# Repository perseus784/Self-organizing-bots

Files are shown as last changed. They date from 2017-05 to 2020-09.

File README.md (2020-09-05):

# About  

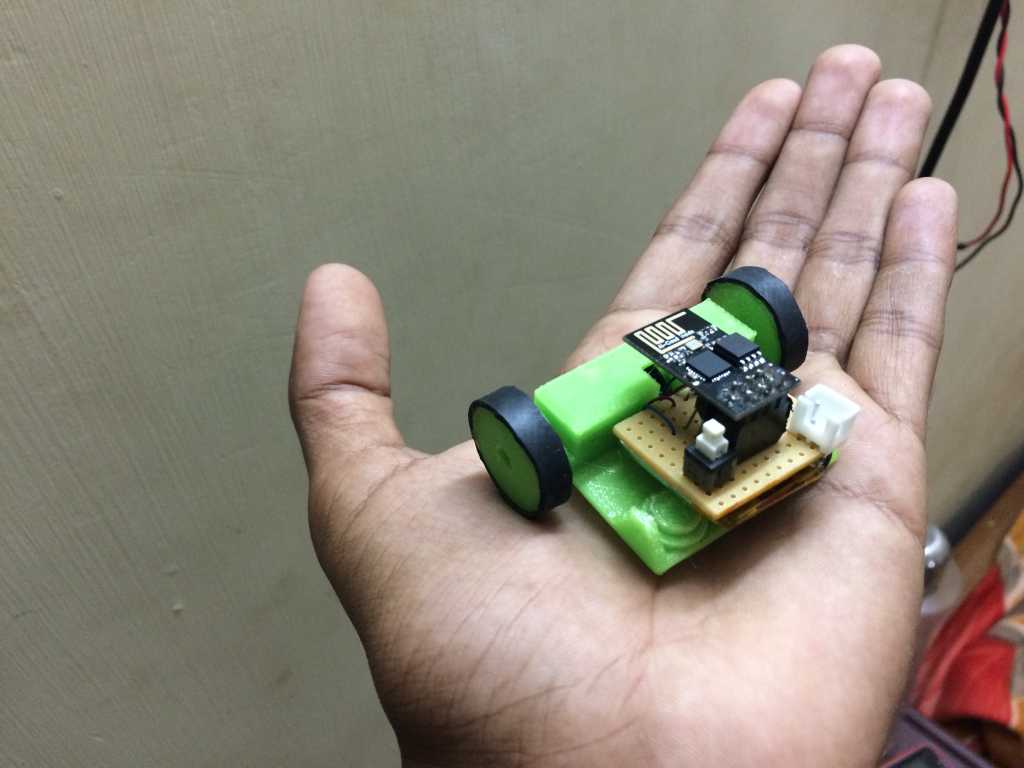
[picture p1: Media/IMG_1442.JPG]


A group of small robots capable of assembling themselves built using ESP8266 wifi module and Python.
The platform consists of a collection of custom-designed wheeled robots each 41x35 mm in dimensions, a Wi-Fi module, and object tracking using image processing techniques. They are controlled by custom written algorithms and python libraries. The project illustrates the potential of group interface through a set of algorithms implemented with custom designed robots, and discuss general design considerations unique to collective intelligence.

## Design Consideration:
 All the parts, modelling, circuits were mainly based on the making the robot as small as possible with the technology that is available in the vicinity. It was constrained by cost, time and availability of the hardware in the geography. Most of the struggle and research went into choosing and making the parts as simple and effective as possible. The finalized design was a product of numerous iteration of protypes in software and hardware level. Making the circuitary small at the same time not too heavy for the motor was a challenge and even that went through a lot of prototyping and expermentation. 
 
<br> 

# Key Features:
* 41x35 mm in dimensions.
* Controlled using WiFi.
* Cheap (around $25). Maybe even cheaper if mass produced.
* 3D files provided.
* Contour tracking
* Path planning
* Simple circuit design

## EXISTING SYSTEM:  
**Zooids:** The project is executed by students of Stanford University. The system introduced swarm user interfaces; It is an open-source open-hardware platform for developing tabletop swarm interfaces. It consists of a collection of custom-designed wheeled micro robots each 2.6 cm in diameter, a radio base-station, a high speed DLP structured light projector for optical tracking, and a software framework for application development and control.

**Kilobots:** Kilobots are done by students of Harvard University. Kilobots should be operated on a smooth, flat surface to ensure proper robot mobility. To aid communication, the surface should be glossy or reflective. The robots beneath the overhead controller in a about a one meter diameter region will be able to receive messages.

## PROPOSED SYSTEM:

On basis of the above survey and after referring various technical papers a new and innovative project idea was developed. The aim of the project "Self organized robots" was to build a group of robots which would construct an input schematic given by the user on a given platform.

The project included study of various fields in Electronics and Computer Science such as Machine Learning, Collective Intelligence, Embedded Systems, Wireless Sensor Networks and Computer Networks. It included Wireless communication between the robots. It consisted of a group or swarm of robots which were guided by a server using various algorithms programmed in its micro-controller. The robot tracking is done by using image processing technique.

## TOOLS

The greatest difficulty faced in the whole system is to make the size of each robot as small as possible. It required building custom designs for the robots and rapid prototyping is employed for the modifications based on practical implementations.

## Hardware

### Battery

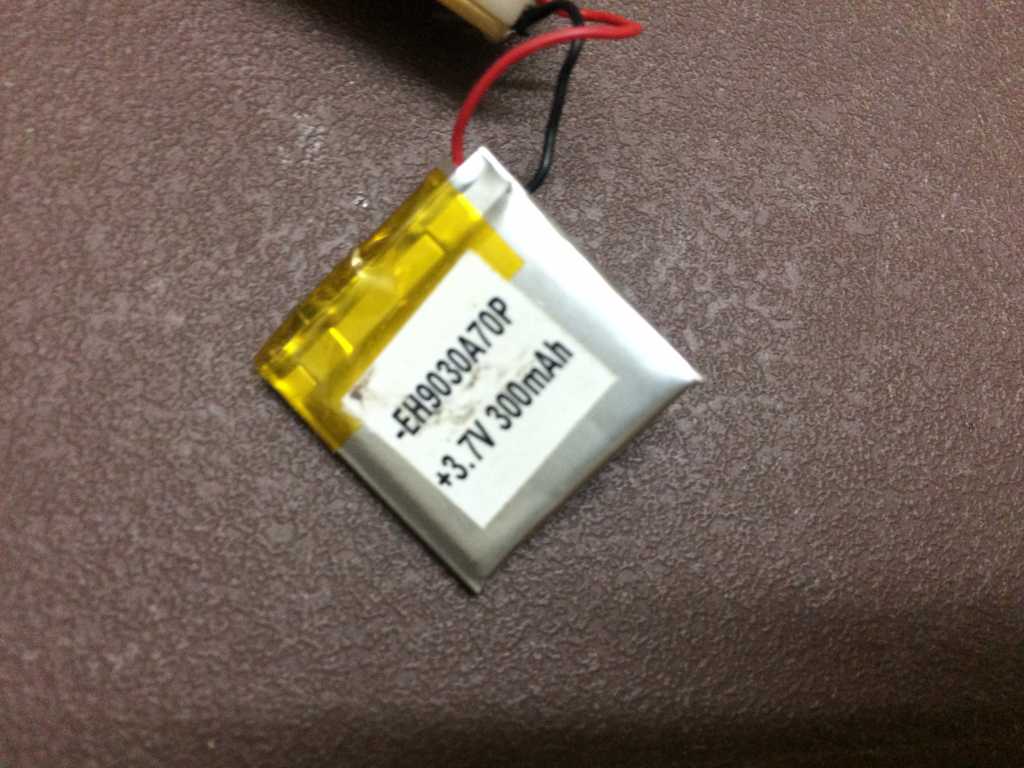
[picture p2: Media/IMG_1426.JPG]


A  Rechargeable Lithium-Polymer battery cell is used to power the entire robot. It has the technical specifications of 3.7v with 200mAh capacity and 20C discharge rate. This optimum design of battery not only helps in keeping the robotic structure  in less weight and small size but also supplies required power efficiently. A single charge of the battery can run the robot for around 20 minutes of continues usage and 1 hour of idle standby. 
<br>

### Coreless DC motor

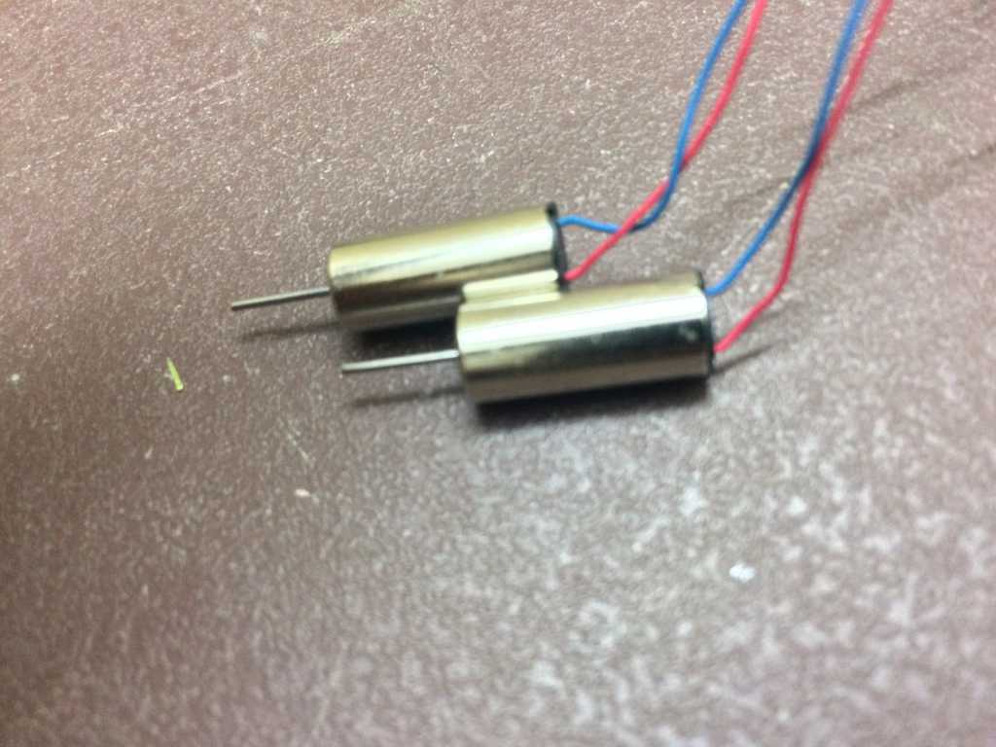
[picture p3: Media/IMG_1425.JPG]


Two coreless DC motors are being employed since it is a two wheeled robot. This two wheeled construction of the robot gives it a 3-degree locomotion i.e. it can move in forward, right and left directions. The motor’s specifications are 3.3v and 0.1A. The motor is specifically selected for its high acceleration and smaller size. It is of size 16*7mm in dimensions.   
<br>

### ESP8266 Wi-Fi Controller

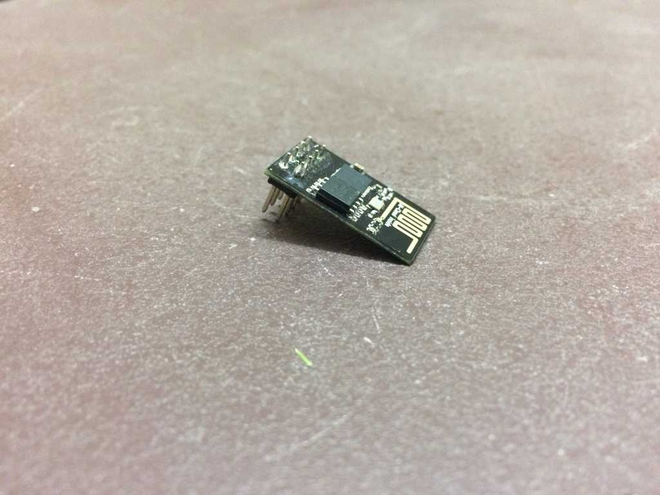
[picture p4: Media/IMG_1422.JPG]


The ESP8266 Wi-Fi Module is a self contained Microcontroller with inbuilt Wi-Fi options. It can establish new networks and also able to connect to already available networks. It has a very compact design with two GPIO pins which makes it the most suitable board for this project. It can be easily programmed by C language Arduino IDE.  
<br>

### BS170 N-Channel MOSFET

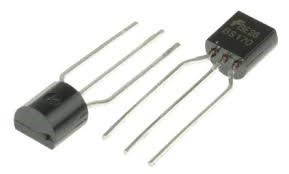
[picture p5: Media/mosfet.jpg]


The BS170 is a logic level MOSFET, which is capable of showing qualities of the higher rating MOSFETs in small signal applications. This property of it used to select it for the switching purpose of the motor using the microcontroller. It has a specification of Vds= 60v and Id= 500 mA.  
<br>

## Software level stuff:
* Python
* Matplotlib
* OpenCV
* Algorithms
* Swarm algorithms
* Socket programming -web services
* Arduino esp8266 programming
* Structural algos
* Clustering
* KNN
* Heirarchical clustering

## 3D Printing 

### SolidWorks Software



SolidWorks is a solid modeler, and utilizes a parametric feature-based approach to create models and assemblies. Building a model in SolidWorks usually starts with a 2D sketch and 3D model can be derived later. The sketch consists of geometry such as points, lines, arcs, and spines. Dimensions are added to the sketch to derive the required 3D model.
The 3D model based on the spatial requirements which has been done using the SolidWorks software is displayed below,

3D Printing is done using 3D Printer. The 3D printer used for prototyping is WANHAO Duplicator. The WANHAO Duplicator makes solid, three-dimensional objects out of melted WANHAO PLA (PolyLactic Acid) Filament. 3D model derived from SolidWorks is translated into instructions for the WANHAO Duplicator and sent to the machine via USB cable or SD Card. Then the WANHAO Duplicator heats the WANHAO PLA Filament and squeezes it out through a nozzle to make a solid object layer by layer. This technique is called fused deposition modeling (FDM).

<p align="left">
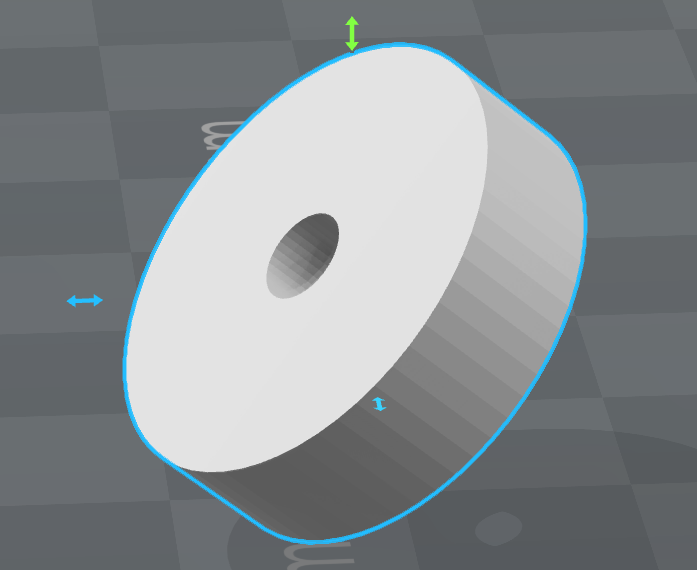
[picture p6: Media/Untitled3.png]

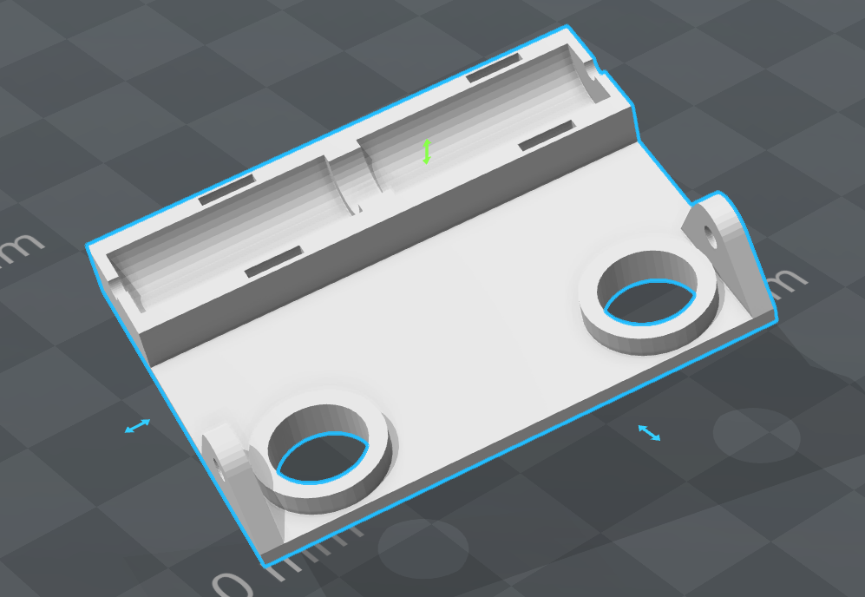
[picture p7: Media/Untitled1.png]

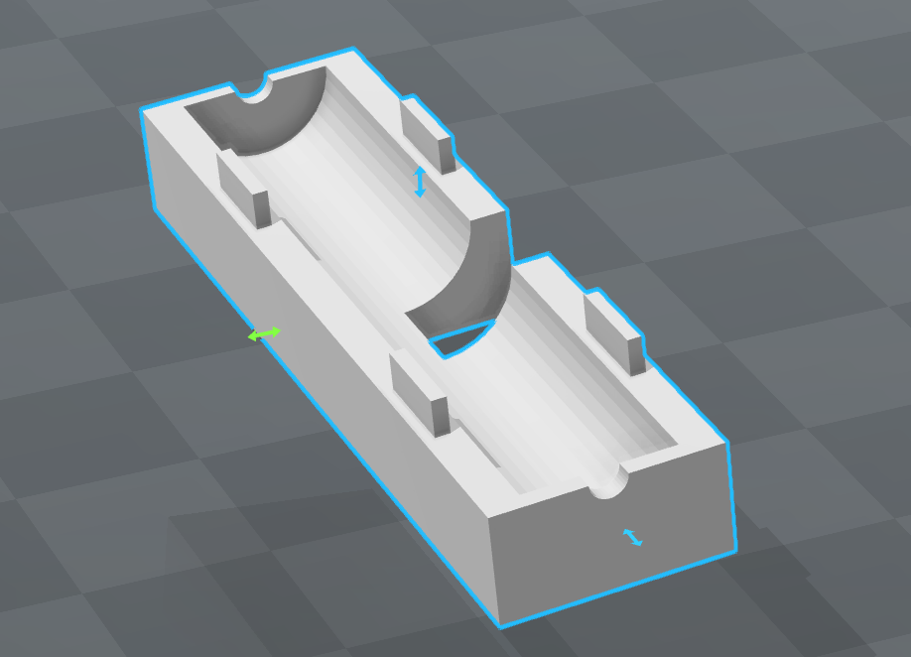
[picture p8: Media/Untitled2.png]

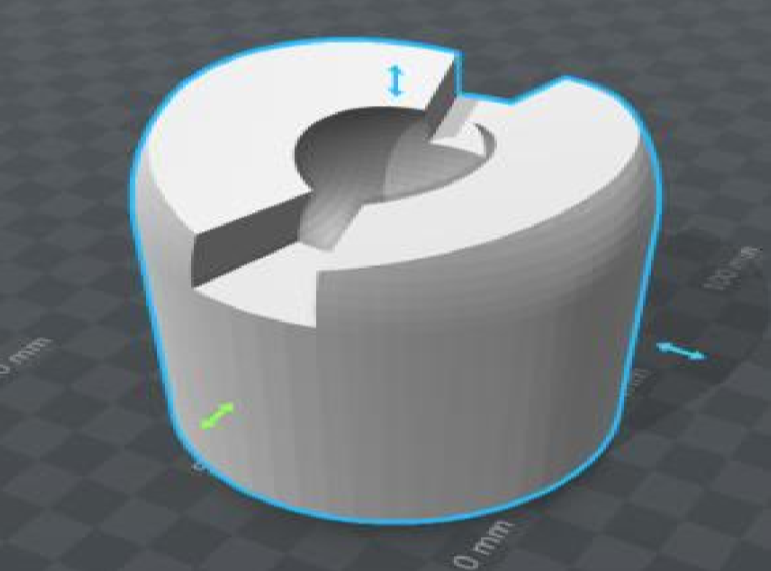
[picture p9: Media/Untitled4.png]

</p>

### Circuit Design

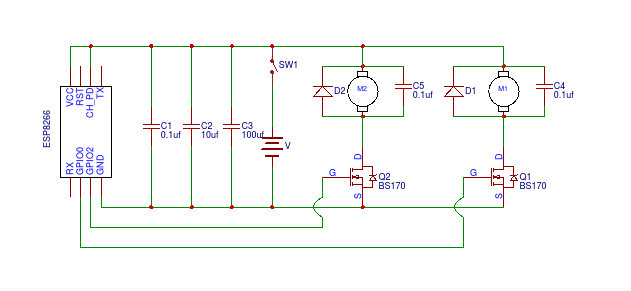
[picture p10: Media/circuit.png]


The circuit is designed mainly on the consideration of simplicity and smallest size possible. So, very basic components are only used in the electrical circuit.

## IMPLEMENTATION

### Hardware Implementation

**3D printed parts ready for assembly:**
                                                                                                                                      
<p align="left">
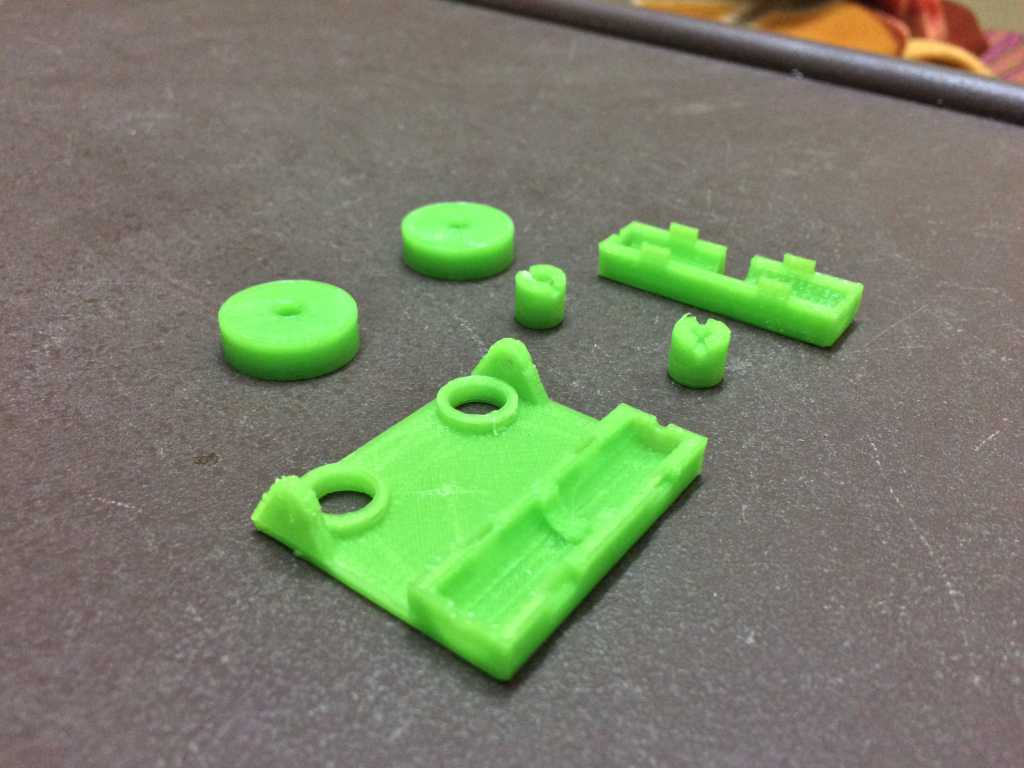
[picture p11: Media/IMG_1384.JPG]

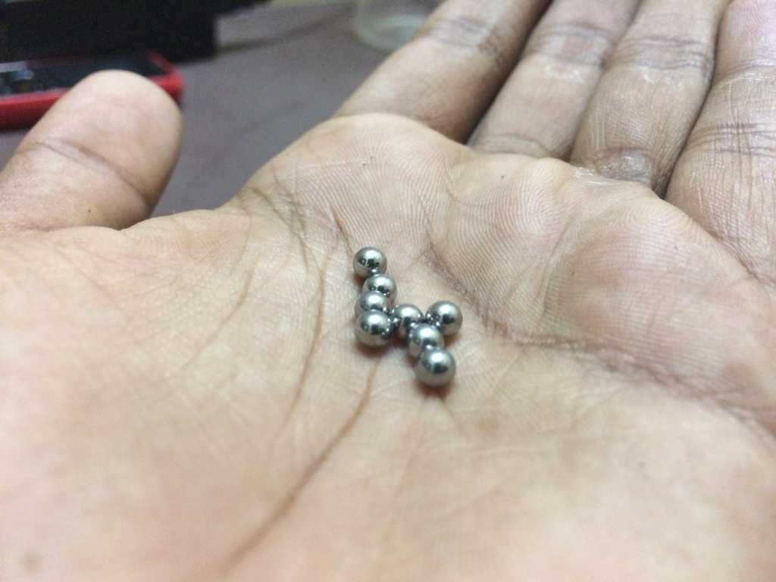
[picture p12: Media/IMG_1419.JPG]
 

</p>

**Electrical Circuit**

<p align="left">
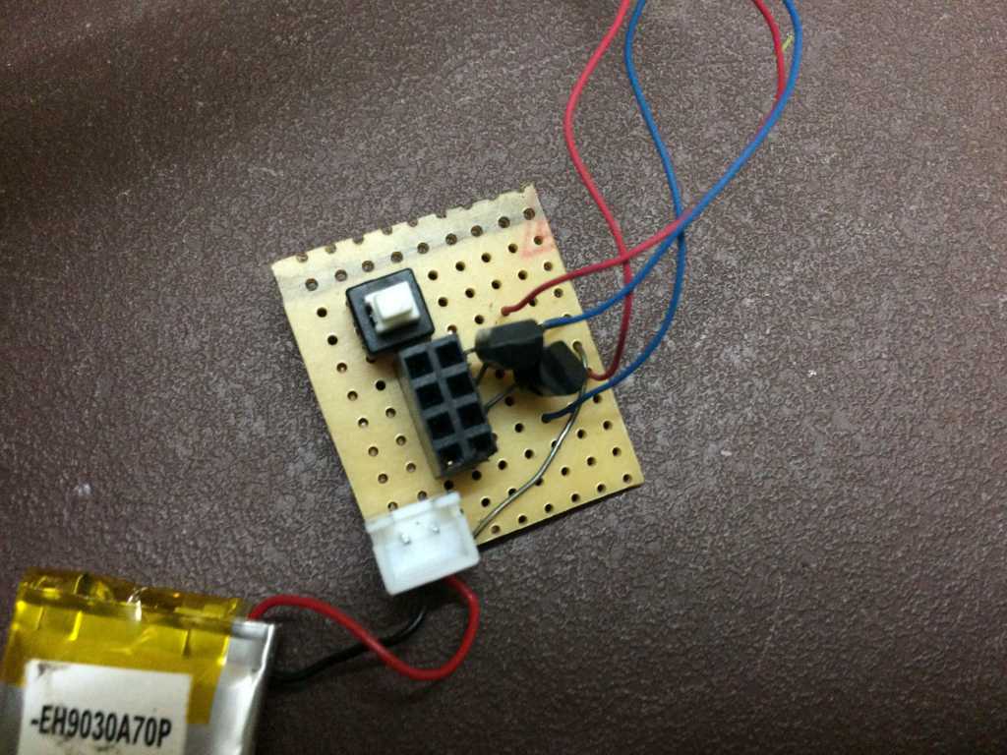
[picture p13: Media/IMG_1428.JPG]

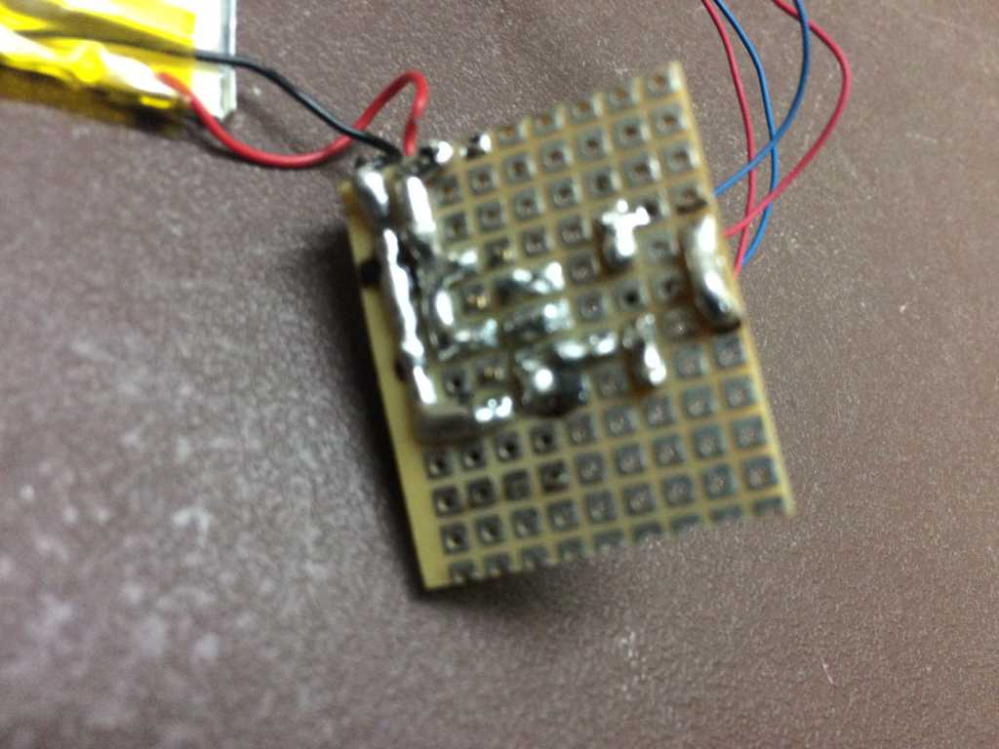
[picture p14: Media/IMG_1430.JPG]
 
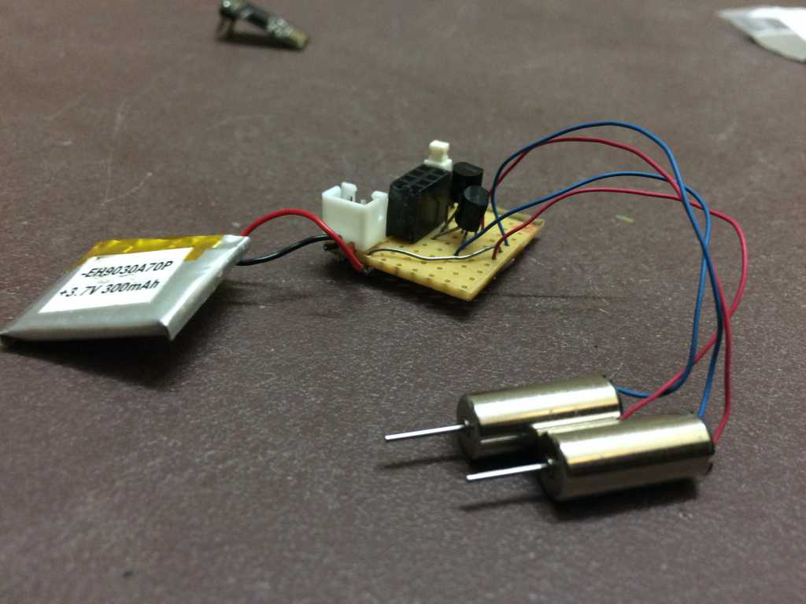
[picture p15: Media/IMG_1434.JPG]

</p>

**Final Product and Swarm Group**

<p align="left">
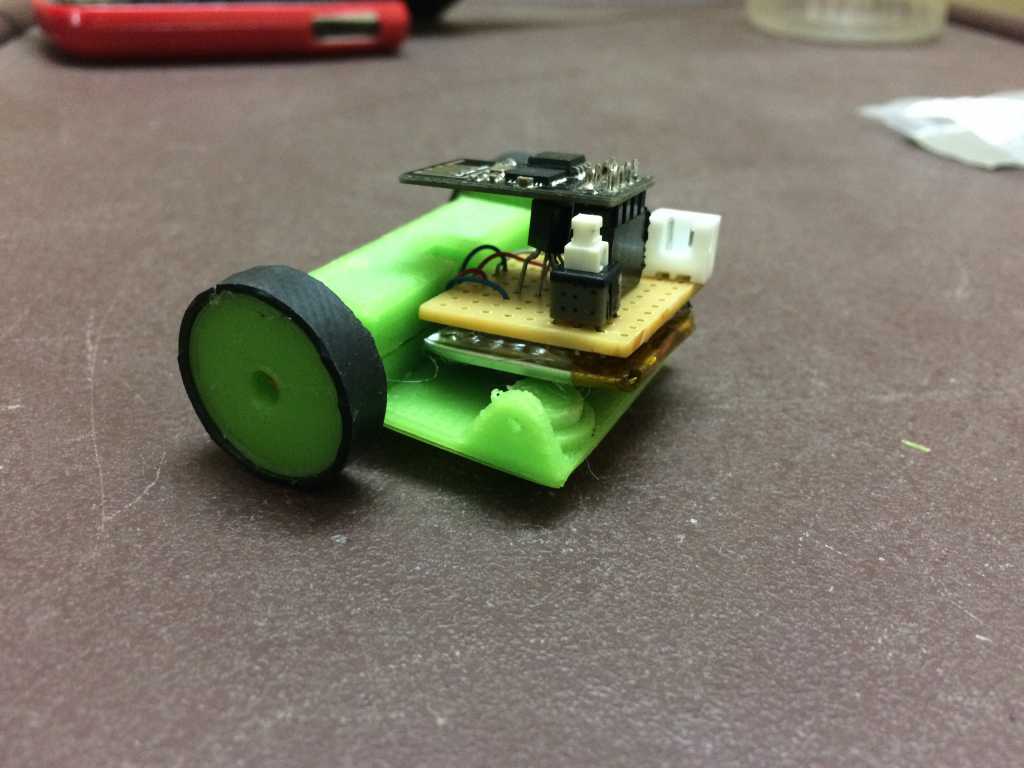
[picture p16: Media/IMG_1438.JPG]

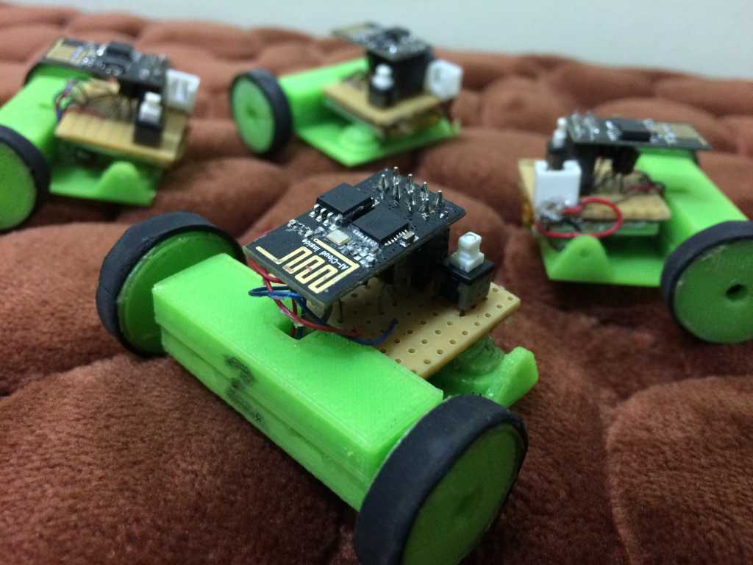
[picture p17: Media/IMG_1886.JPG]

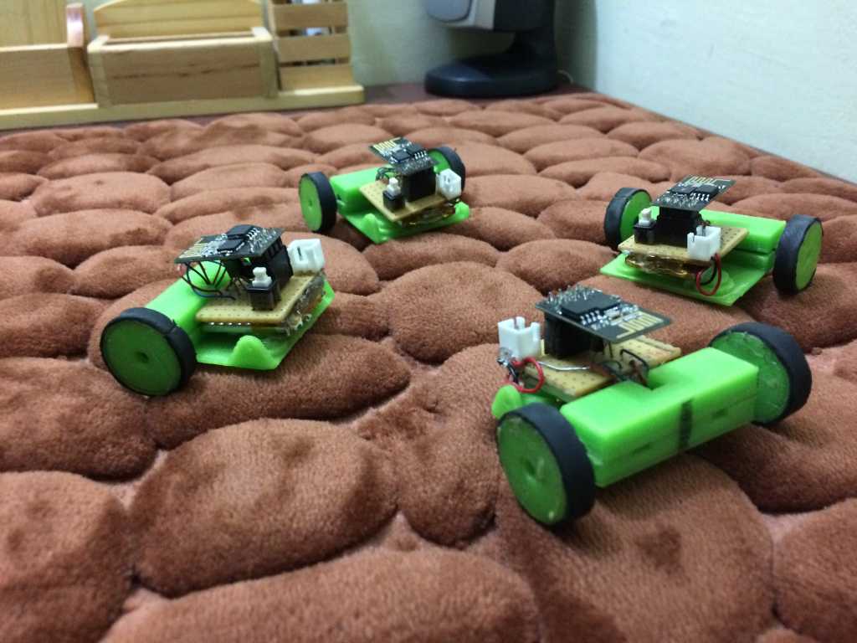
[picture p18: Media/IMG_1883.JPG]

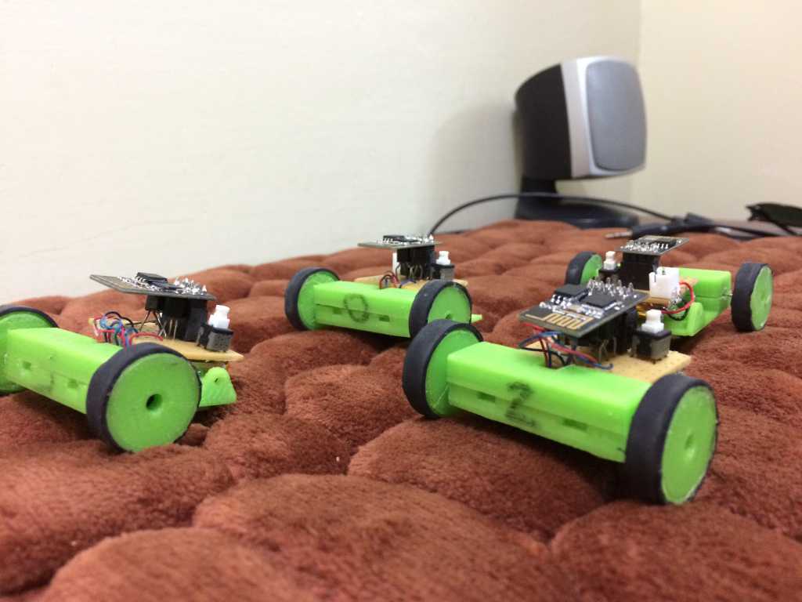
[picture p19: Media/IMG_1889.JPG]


</p>

# WORKING

**Architecture:**
 <p align="center">
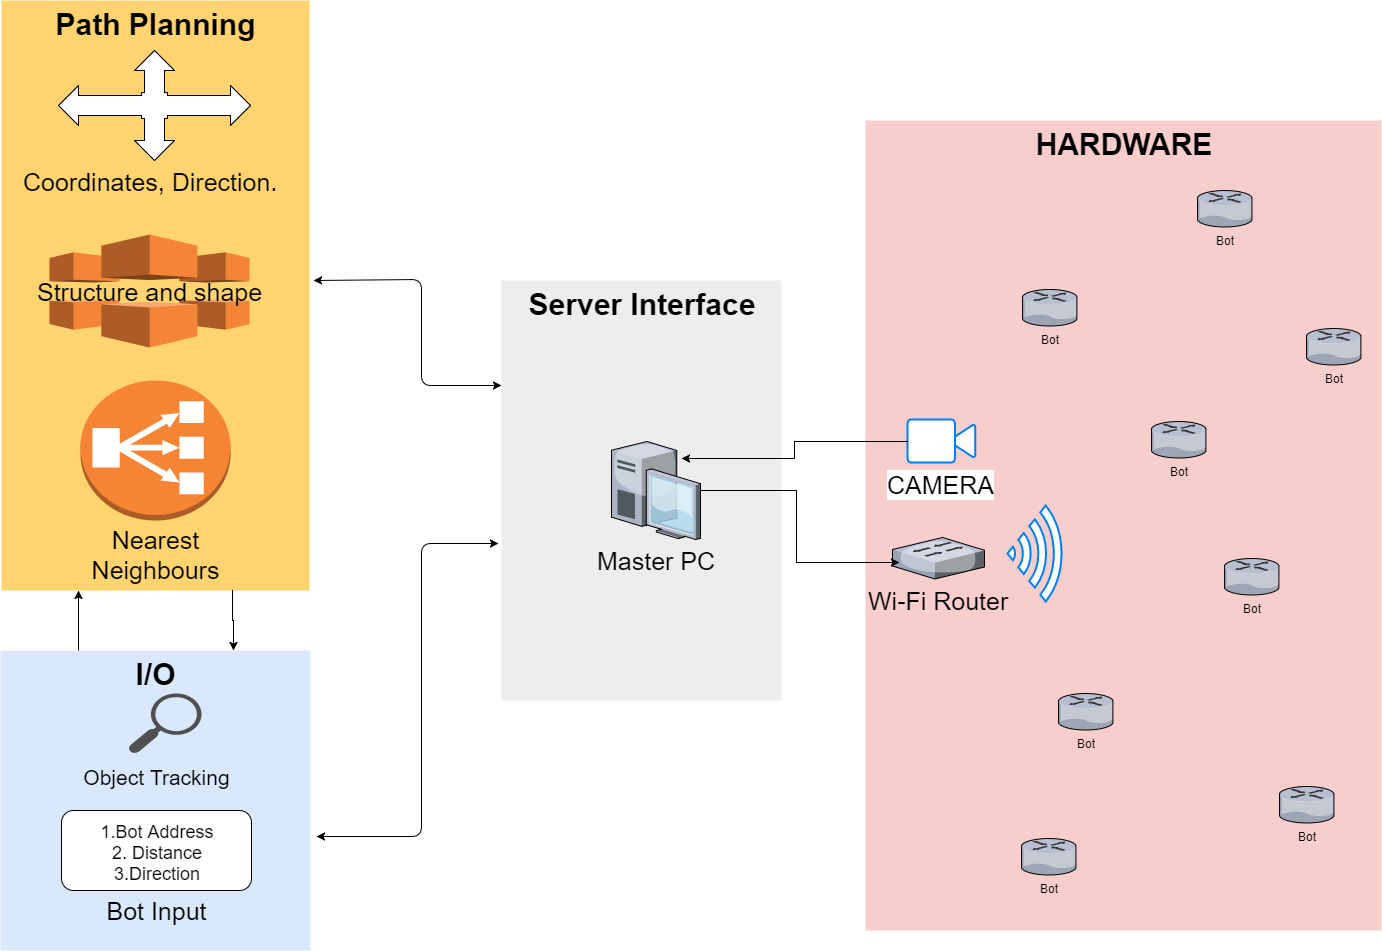
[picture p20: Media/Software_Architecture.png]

</p>

The communication between the robots and the master is via a secure Wi-Fi local network. This local network paves way for two way communication between the master and the slaves. The master is usually a PC with a custom built program running on it. This master program governs the position, movement and arrangement of the robots.

 A video camera is used to keep track the position of the robots using color detection methods and it’s a continuously running loop once the program has started until the goal is achieved.

**Robot Position Tracking:**

<p align="center">
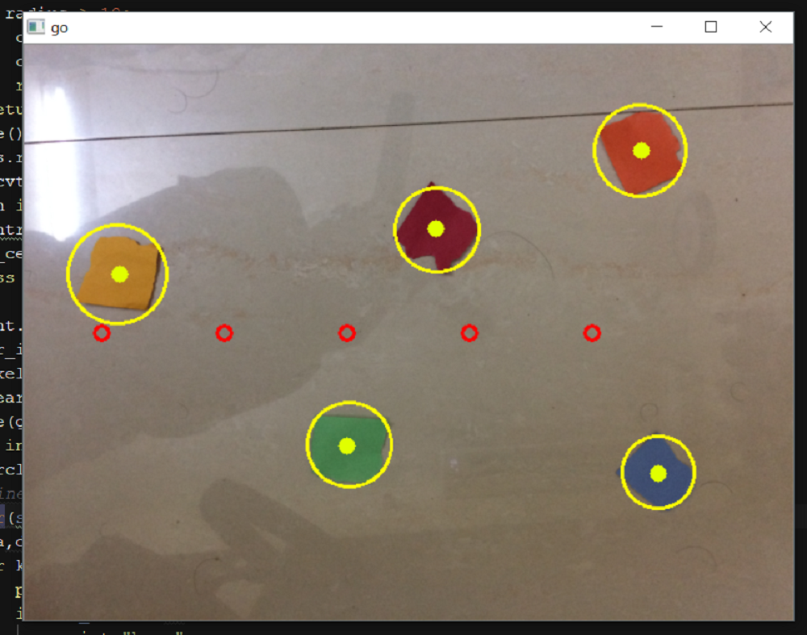
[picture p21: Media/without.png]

</p>

Robots are tracked with the help of a python library named openCV. It is highly used in the fields of image processing. Each robot is given a separate color on top of it so, a simple color identification technique is used to find the color tag of the robot. Each color tag represents a unique bot ID from which the Wi-Fi address of the robot can be found.
The image contains a color detection sample for 5 different colors simultaneously and also using image processing the centers of the each color contours are also found. This gives a great way of robot tracking even in very ruff conditions.

Even though robots are localized, it is a difficult problem to find the orientation of the robots. To find orientation of the robots the following method is used.
* A right angled triangle is sticked on the top of the robot than a previously shown circle identifier.
* first we have to find the hypotenuse of the triangle, it can be done using opencv coutour finding, Coner-Harris methos and Heirarchical clustering. It is clearly explained here -> [Finding Hypotenuse](https://github.com/perseus784/Shape-Finder).
* Once we find the hypotenuse, we can easily know to which angle it is deviated from the bisector of the display. Then we can orient the robot to that angle and adjust to align perpendicular to the bisector.

<p align="left">
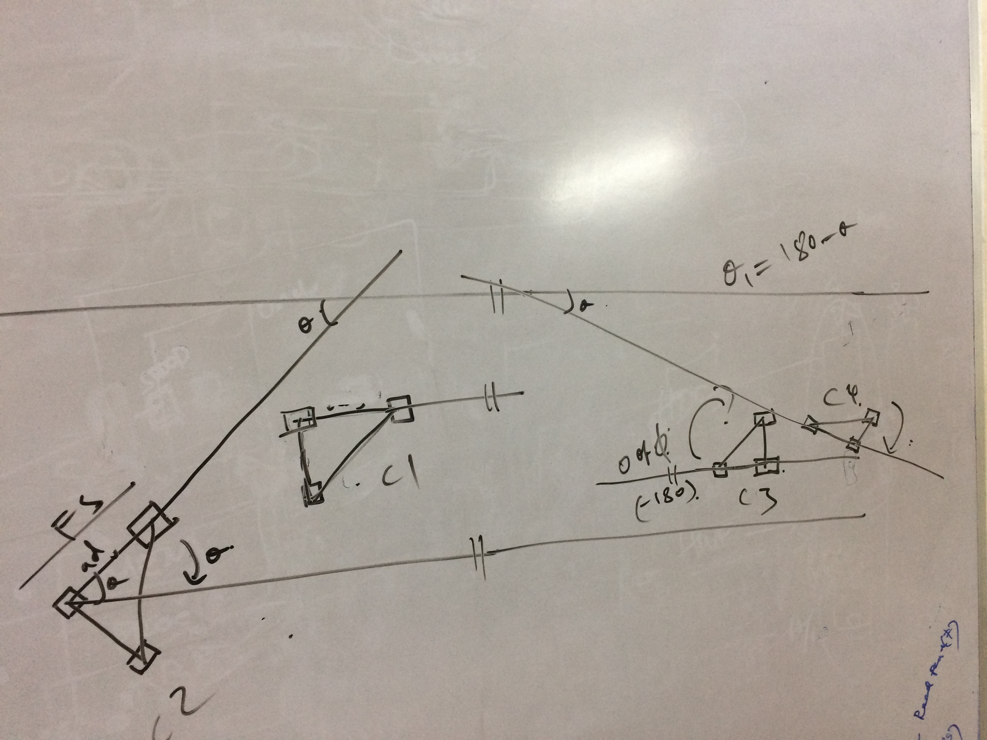
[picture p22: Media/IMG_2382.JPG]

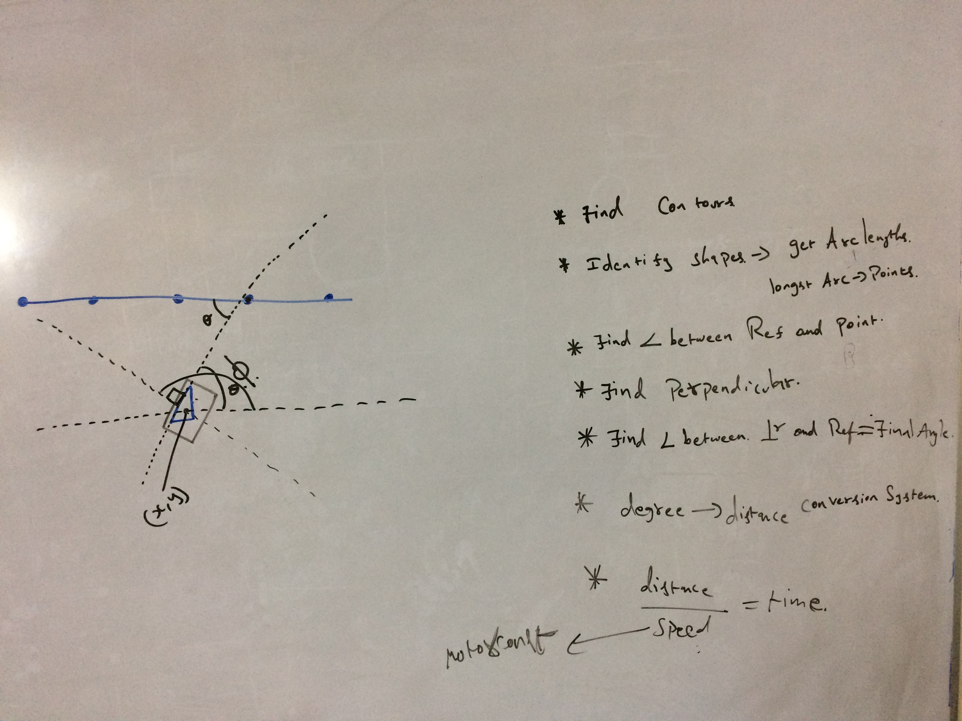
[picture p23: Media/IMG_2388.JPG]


</p>

## Skeleton Structures

The algorithms are designed in such a way that it is adaptive to any given area and form the same structure. When the user gives any surface as input the program calculates the skeletal structures and minimal number of robots for that structure. We have implemented two skeletal structures as pre defined default structure, if needed in future it is very trivial to add more and more skeletal structures to the program.

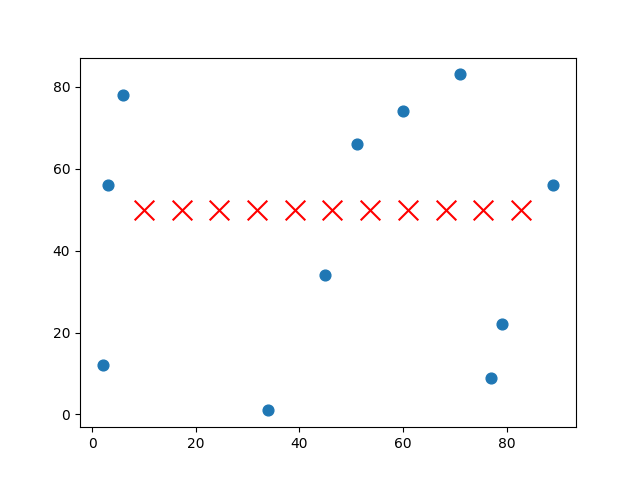
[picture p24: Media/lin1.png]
  

<br> 

**Line structure** 

The blue points in the picture indicate the robots which are placed in a random manner.
The Red Cross indicates the target skeleton points which are generated from the custom built algorithm for line formation for any given plane.
<br>
<br>
<br>
<br>
<br>
<br> 
<br>

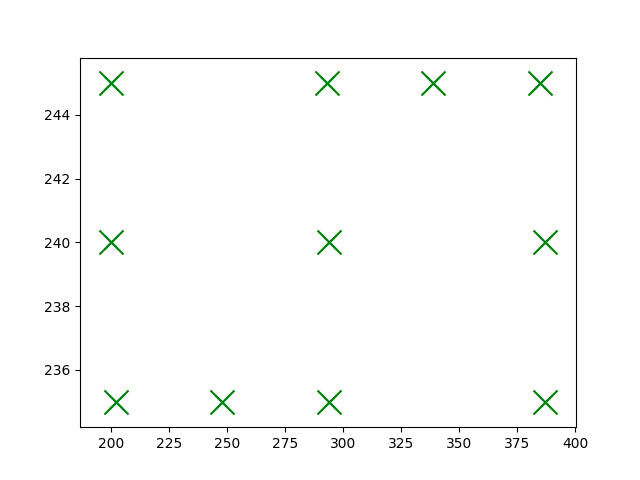
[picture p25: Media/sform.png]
 

<br> 
<br> 

**S-structure** 

The green cross indicates the target skeleton points which are generated from the custom built algorithm for ‘S’ formation for any given plane. 
<br>
<br>
<br>
<br>
<br>
<br>
<br>

## Path Planning:

After acquiring both the current position and destination points, the algorithm plans the path for the robots to move in its degree of freedom. This process of path planning happens in two stages,
Initially, the bot points are allocated to random points in the skeleton and the distance is calculated. This follows no specific format or computation so it’s a quick way but this causes the total distance travelled by the robots to be larger. This practice makes the whole process very time consuming and it wastes a lot of battery power. So, an algorithm is employed to rectify this disadvantage.

## Finding the nearest point:

The path derived without using nearest neighbour algorithm. By observation, it can be seen that the distance travelled by the robots is much longer. So, applying nearest neighbor algorithm the following paths are obtained which are more optimum to the given set of paths.

The distance is found for all the robots given and the target point is selected for a particular robot by selecting the smallest available Euclidean distance that had been found before. The Euclidean distance can be found by the following formula,
 <p align="center">

</p>
                                    
                                    Euclidean distance = sq root (bot point – target point).
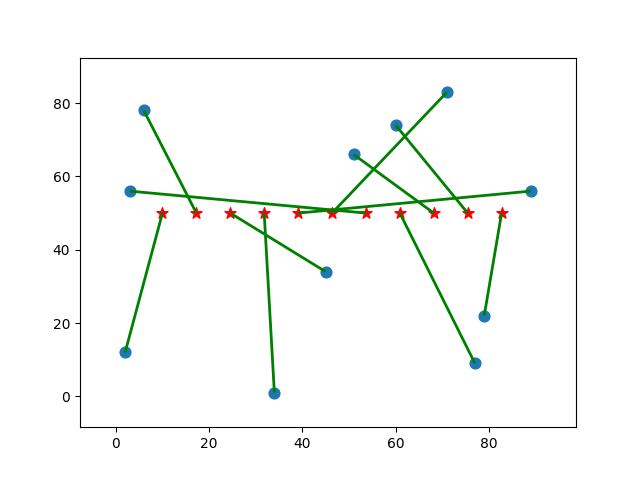
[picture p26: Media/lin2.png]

<br> 
<br>
In this picture, the green lines indicate the path traced by the robots for the line formation after applying the nearest neighbouring algorithm.
<br>
<br>
<br>
<br>
<br>
<br>
<br>
<br>
<br>
<br>
<br>

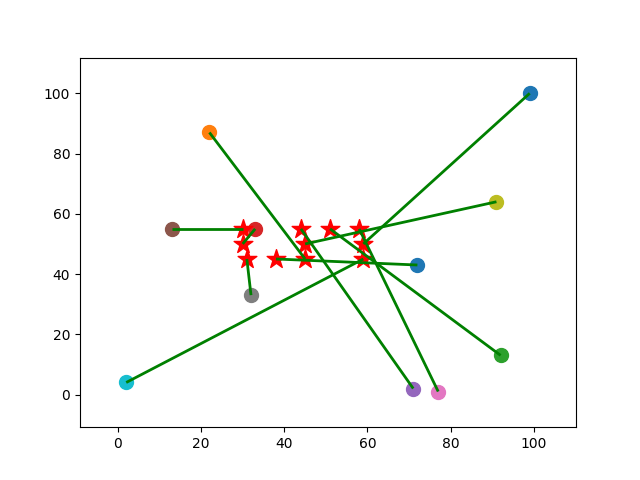
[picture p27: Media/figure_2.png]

<br> 
<br>
The same algorithm is applied for the S-structure formation. The distance is greatly reduced in both the cases.
<br>
<br>
<br>
<br>
<br>
<br>
<br>
<br>
<br>
<br>

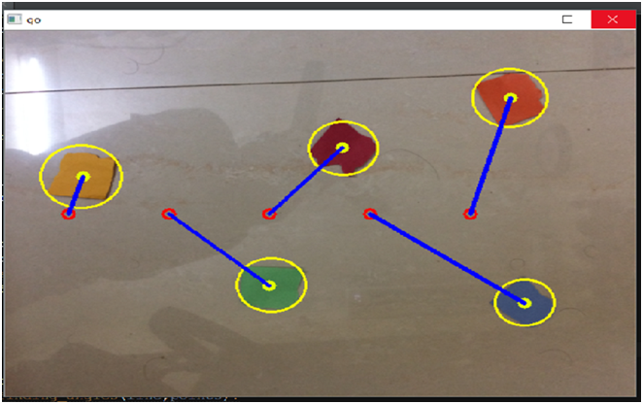
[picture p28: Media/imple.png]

<br>
Real time tracking and application of the nearest neighbor algorithm has been shown this image. The blue lines represent the paths that should be traced down by the robot to attain the optimum point for forming the line structure.
<br>
<br>
<br>
<br>
<br>
<br>
<br>
<br>
<br>
<br>

## Feeding data to the Robots:
<p align="center">
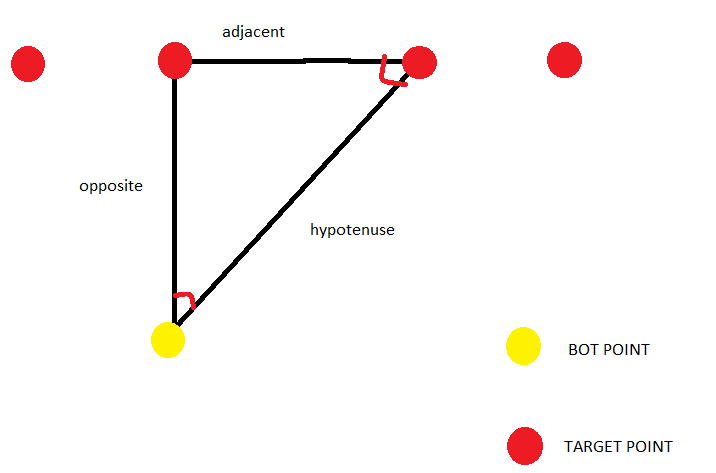
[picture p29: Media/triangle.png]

</p>
The robot should be fed with the data of distance and angle for each specific for the structure formation. So, to calculate distance and angle the following method is used
To find the distance, hypotenuse is found to the triangle formed while adjacent is the median for the whole plane. The angle that to be tilted is found by using the formula,

                                                 α = sin-1(opposite/hypotenuse)

(Distance, α) is appended to a list which contains the same for all other robots. So, the ESP Arduino obtains this distance and angle and facilitates the robot to move in this α direction to that distance. 

<p align="left">
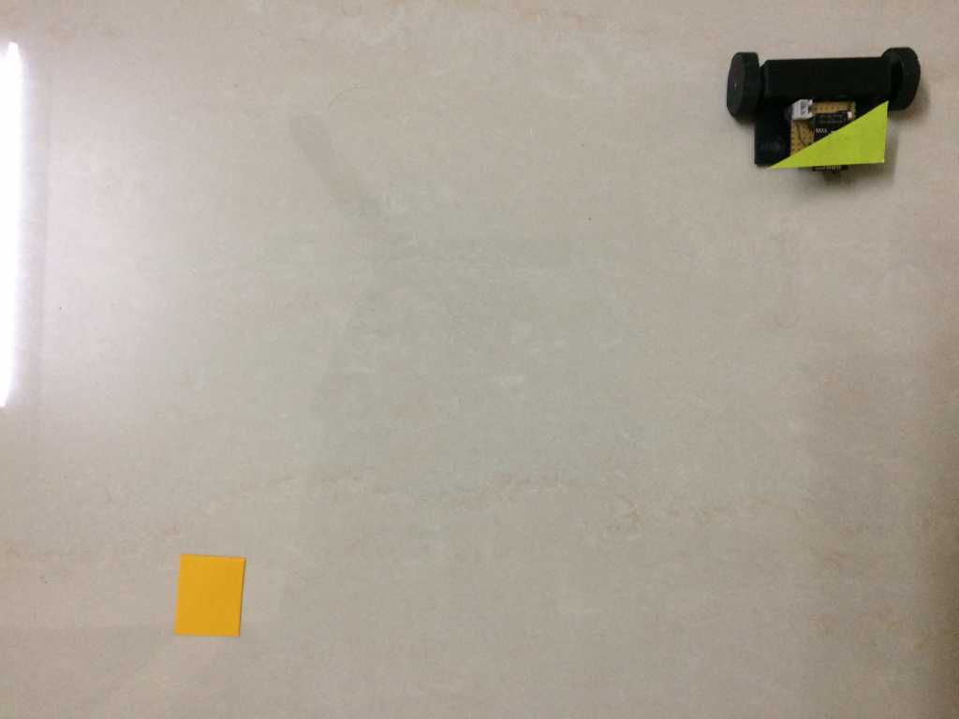
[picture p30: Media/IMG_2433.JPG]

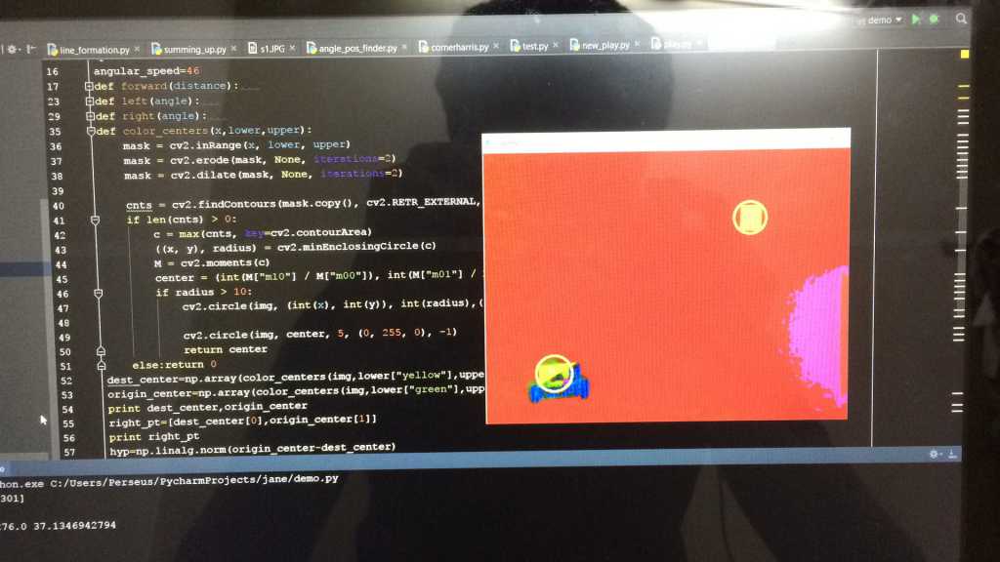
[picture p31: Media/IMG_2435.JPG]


</p> 

# CONCLUSION

After studying different research papers and scientific journals we found that our project “Self Organizing Robots” had many advantages over the other conventional robotics techniques.

Firstly, the small size of the client robot helps us to carry the robots conveniently to any given location to perform work. Secondly, the server which has been developed makes the task of the user to assign work to the robots rudimentary.

Using the concept of ’Collective intelligence’ reduces the cost and  increases the expandability of the robots. A particular robot can be replaced in case of damages instead of  replacing the whole.
In future, size can be extremely reduced and the same algorithm can be implemented irrespective of  their platform. It has vast scopes in various fields such as Medicine, Defence etc.

<p align="center">
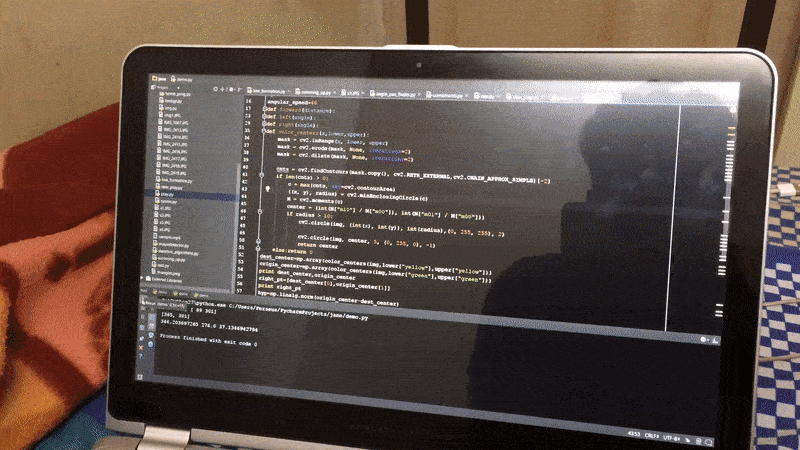
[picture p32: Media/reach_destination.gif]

</p> 

## Updated Bot:
The previous version of it is hard to control because of the coreless motor.
So, it is replaced with Microgearded motors and also the strcuture of the 3D models were also changed to adapt to the new motor size.
Eventhough it made the bot slightly bigger than the previous version, it gives us more control and stability in structure.

**New Model** 
<p align="left">
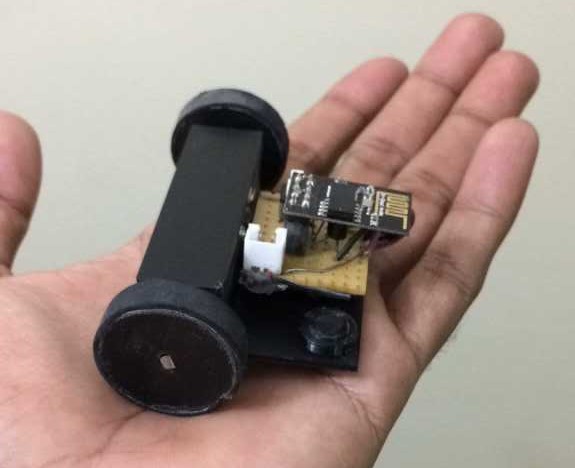
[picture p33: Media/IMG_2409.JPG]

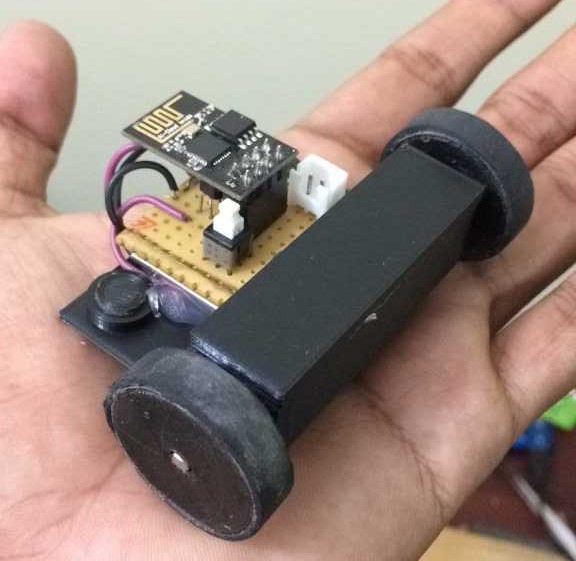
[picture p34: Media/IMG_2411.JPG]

</p>

The updated 3D files can be found [here](https://github.com/perseus784/Self-organizing-bots/tree/master/3D%20model/Version2(Micro%20Geared))

**New Motors**
<p align="left">
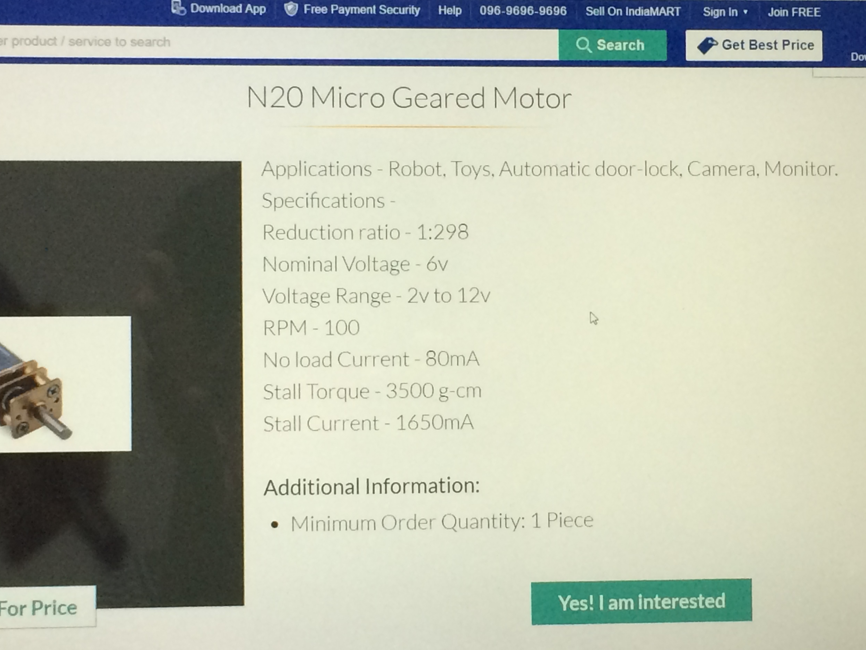
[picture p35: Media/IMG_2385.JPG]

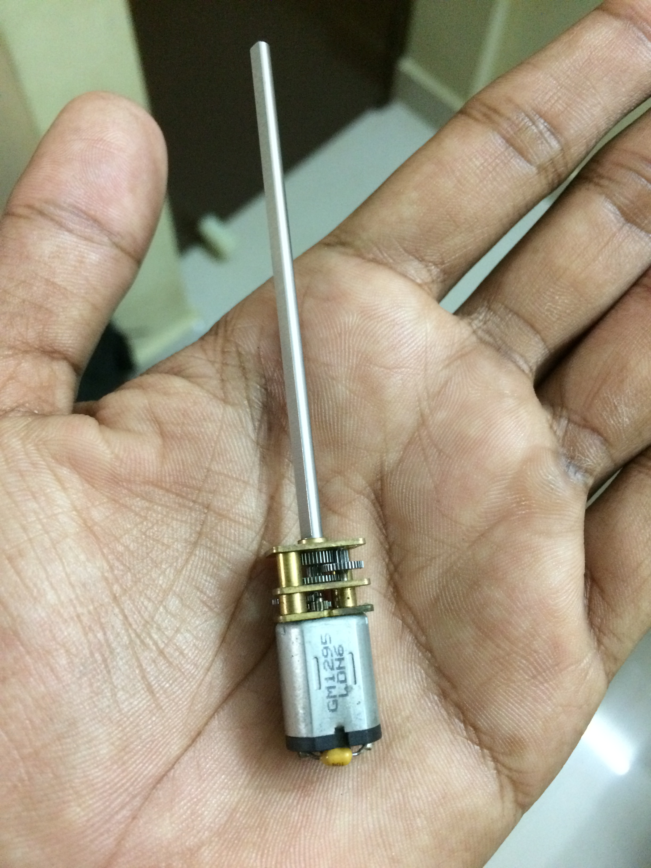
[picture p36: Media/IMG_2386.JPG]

</p> 

The remaining circuitary and other components are all the same. 

## Future Ideas: 

USING ARUCO MARKERS.
EASY TO DETERMNINE AND LOCALIZE THE ROBOTS THAN BEFORE. 
DONT HAVE TO TAKE CARE OF ANYTHING AT ALL

# REFERENCES

## BASE PAPER DETAILS

1.Kilobot: A Low Cost Scalable Robot System for Collective Behaviors Michael Rubenstein, Christian Ahler, Radhika Nagpal IEEE Intl. Conf on Robotics and Automation (ICRA), 2012.

2.Mathieu Le Goc, Lawrence Kim, Ali Parsaei, Jean-Daniel Fekete, Pierre Dragicevic, Sean Follmer. Proceedings of the 29th Annual ACM Symposium on User Interface Software & Technology (UIST 2016), June 2016, Tokyo, Japan. (In press).

## OTHER REFERENCES

1.Collective Transport of Complex Objects by Simple Robots: Theory and Experiments Rubenstein, Cabrera, Werfel, Habibi, McLurkin, Nagpal Intl. Conf. on Autonomous Agents and Multiagent Systems (AAMAS), May 2013.

2.Programmable Self-Assembly in a Thousand-Robot Swarm Michael Rubenstein, Alejandro Cornejo, Radhika Nagpal Science, Vol 345, no 6198, 15 Aug 2014.

3.Rise of the Swarm, Communications of the ACM, 2013. SEAS Article (Kilobots are leaving the nest), 2011 Slashdot Article (Nov 2011).

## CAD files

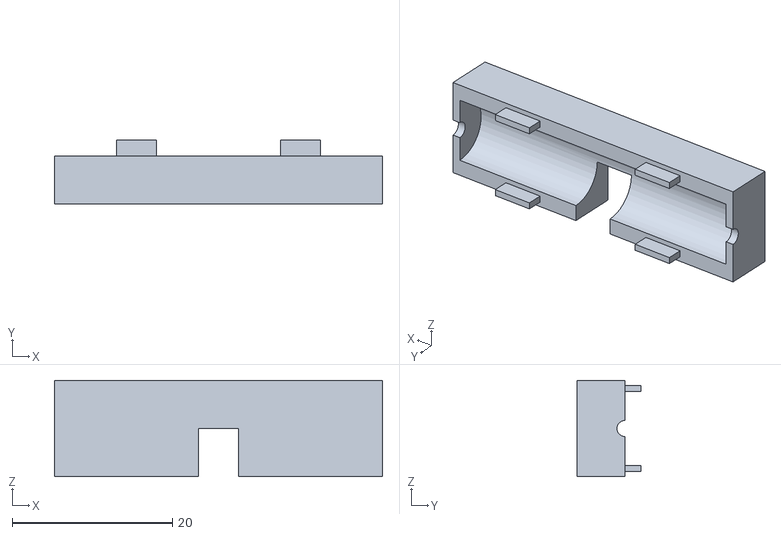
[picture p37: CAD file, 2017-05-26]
3D files/Version1(Coreless motors)/enclosure.STL
41.0 x 8.00 x 12.0

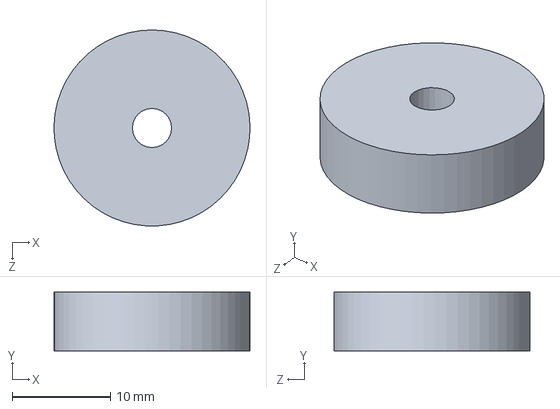
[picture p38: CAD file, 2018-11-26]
3D files/Version1(Coreless motors)/Raw Solidworks files/wheel.SLDPRT
20.0 x 6.00 x 20.0 mm

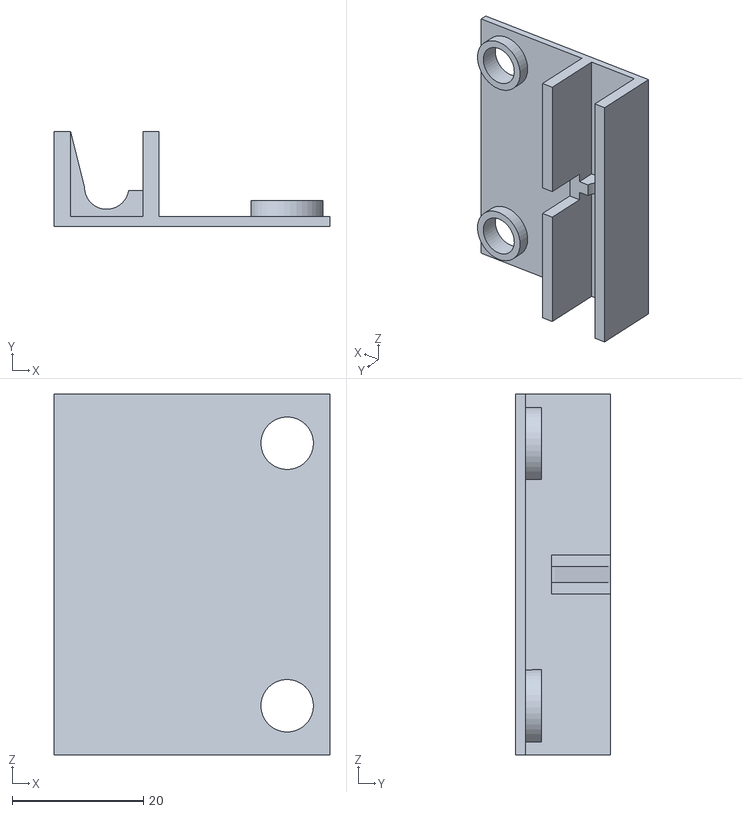
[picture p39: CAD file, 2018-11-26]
3D files/Version2(Micro Geared)/base.STL
42.0 x 14.5 x 55.0

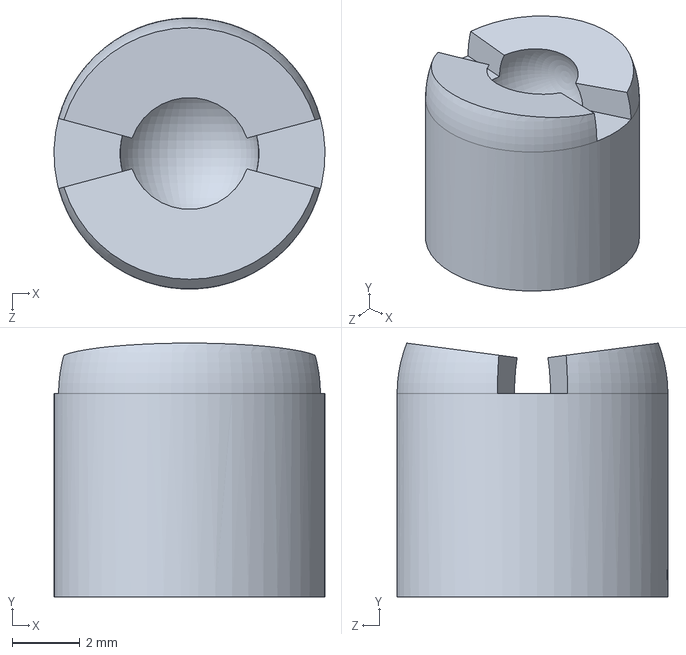
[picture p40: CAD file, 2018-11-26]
3D files/Version2(Micro Geared)/Raw Solidworks files/castor.SLDPRT
8.00 x 7.49 x 8.00 mm

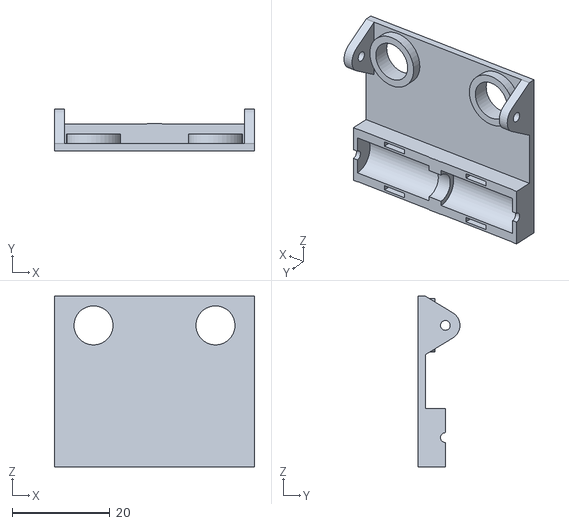
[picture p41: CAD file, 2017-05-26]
3D files/Version1(Coreless motors)/base.STL
41.0 x 8.60 x 35.0

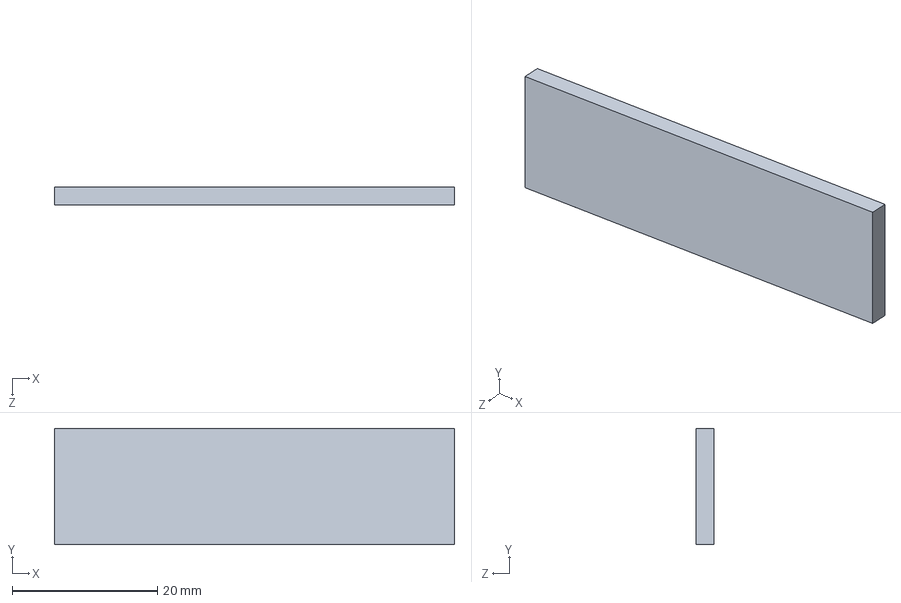
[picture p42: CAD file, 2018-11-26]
3D files/Version2(Micro Geared)/Raw Solidworks files/top.SLDPRT
55.0 x 16.0 x 2.50 mm

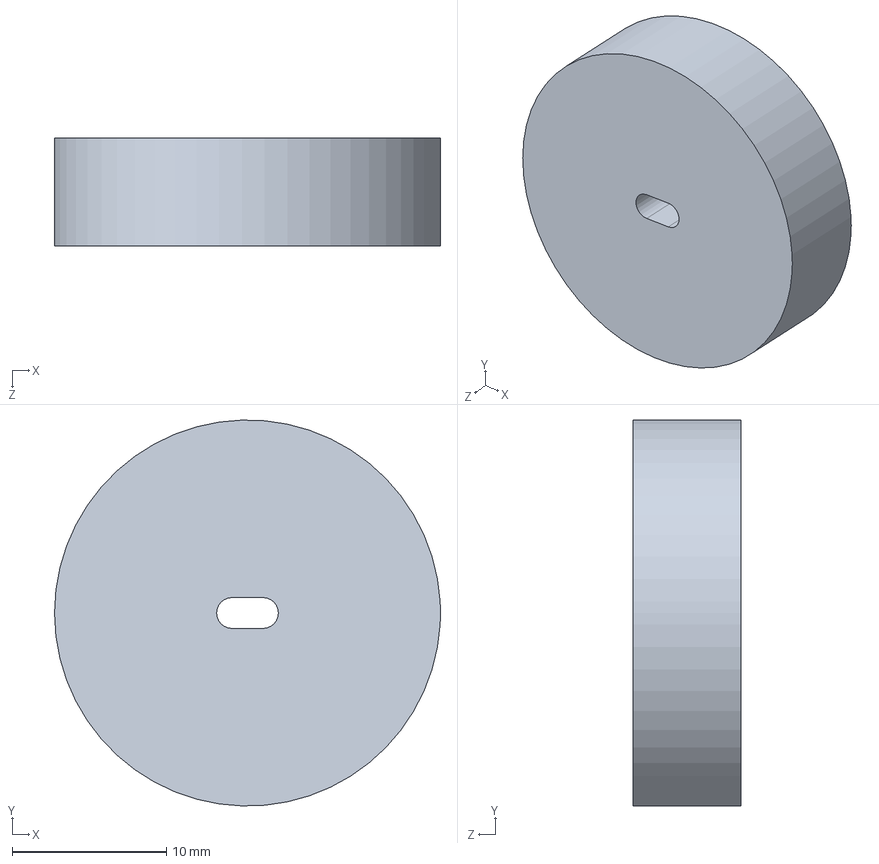
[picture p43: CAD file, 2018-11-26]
3D files/Version2(Micro Geared)/Raw Solidworks files/wheel_new.SLDPRT
25.0 x 25.0 x 7.00 mm

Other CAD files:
3D files/Version2(Micro Geared)/top.STL
3D files/Version1(Coreless motors)/castor.STL
3D files/Version1(Coreless motors)/Raw Solidworks files/base.SLDPRT
3D files/Version2(Micro Geared)/wheel_new.STL
3D files/Version1(Coreless motors)/Raw Solidworks files/enclosure.SLDPRT
3D files/Version1(Coreless motors)/wheel.STL
3D files/Version2(Micro Geared)/castor.STL
3D files/Version2(Micro Geared)/Raw Solidworks files/base.SLDPRT

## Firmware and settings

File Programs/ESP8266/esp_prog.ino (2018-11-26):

#include <ESP8266WiFi.h>
 
const char* ssid = "xxxxxxxx";
const char* password = "xxxxxxxx";
IPAddress staticIP(10,0,0,71);
IPAddress gateway(10,0,0,1);
IPAddress subnet(255,255,255,0);
int ledPin = 0;
int ledPin1 = 2;
WiFiServer server(80);
 
void setup() {
  Serial.begin(115200);
  delay(10);
 
  pinMode(ledPin, OUTPUT);
  pinMode(ledPin1, OUTPUT);
  digitalWrite(ledPin, LOW);
  digitalWrite(ledPin1, LOW);
 
  // Connect to WiFi network
  Serial.println();
  Serial.println();
  Serial.print("Connecting to ");
  Serial.println(ssid);
 
  WiFi.begin(ssid, password);
  WiFi.config(staticIP, gateway, subnet);
  while (WiFi.status() != WL_CONNECTED) {
    delay(500);
    Serial.print(".");
  }
  Serial.println("");
  Serial.println("WiFi connected");
 
  // Start the server
  server.begin();
  Serial.println("Server started");
 
  // Print the IP address
  Serial.print("Use this URL to connect: ");
  Serial.print("http://");
  Serial.print(WiFi.localIP());
  Serial.println("/");
 
}
 
void loop() {
  // Check if a client has connected
  WiFiClient client = server.available();
  if (!client) {
    return;
  }
 
  // Wait until the client sends some data
  Serial.println("new client");
  while(!client.available()){
    delay(1);
  }
 
  // Read the first line of the request
  String request = client.readStringUntil('\r');
  Serial.println(request);
  client.flush();
 
  // Match the request
 
  int value = LOW;
  if (request.indexOf("/LED=ON") != -1)  {
    digitalWrite(ledPin, HIGH);
    digitalWrite(ledPin1, HIGH);
    value = HIGH;
  }
  if (request.indexOf("/LED=OFF") != -1)  {
    digitalWrite(ledPin, LOW);
    digitalWrite(ledPin1, LOW);
    value = LOW;
  }
  if (request.indexOf("/LED1=ON") != -1)  {
    digitalWrite(ledPin, HIGH);
    digitalWrite(ledPin1, LOW);
    value = HIGH;
  }
  if (request.indexOf("/LED2=ON") != -1)  {
    digitalWrite(ledPin1, HIGH);
    digitalWrite(ledPin, LOW);
    value = HIGH;
  }
// Set ledPin according to the request
//digitalWrite(ledPin, value);
 
  // Return the response
  client.println("HTTP/1.1 200 OK");
  client.println("Content-Type: text/html");
  client.println(""); //  do not forget this one
  client.println("<!DOCTYPE HTML>");
  client.println("<html>");
 
  client.print("Led pin is now: ");
 
  if(value == HIGH) {
    client.print("On");
  } else {
    client.print("Off");
  }
  client.println("<br><br>");
  client.println("&emsp;<a href=\"/LED=ON\"\"><button>FORWARD </button></a><br />");
  client.println("<a href=\"/LED2=ON\"\"><button>LEFT </button></a>");
  client.println("&ensp;<a href=\"/LED1=ON\"\"><button>RIGHT </button></a><br />");
  client.println("&emsp;&ensp;&nbsp;<a href=\"/LED=OFF\"\"><button>STOP </button></a>");  
  client.println("</html>");
 
  delay(1);
  Serial.println("Client disonnected");
  Serial.println("");
 
}
 

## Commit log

2017-05-26 Add files via upload
    3D models of the prototypes.
    Former-commit-id: 9af02b4925da6febfe35dc0c550365d1e54879cf
    [base.STL, castor.STL, enclosure.STL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]
2018-11-26 added files
    Former-commit-id: 09a2358fa08de97d6cbb1a9264f8531a412623ff
    Former-commit-id: 6a6da6763f2a61b8ee05e81f8906be92a7a91299
    [assembly - Body-1.STL, assembly - Enclose-1.STL, assembly - wheel 1-1.STL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]
2018-12-06 cleaned
    Former-commit-id: d2d3b506accf4801b9007f8312053c0a40a0d2b4
    Former-commit-id: f4c29e3f40e16ecd0f8d18e00e69985d5d38b38c
    [assembly - Body-1.STL, assembly - Enclose-1.STL, assembly - wheel 1-1.STL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]
2018-12-07 media update
    Former-commit-id: 992b56d21a790a8729606346952796f62f7b0637
    Former-commit-id: f6adda2b69c97f1ca420b8d0737f8903f0aa01ae
    [base.SLDPRT, base.STL, castor.SLDPRT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]
2018-12-08 readme
    Former-commit-id: 1a9e6ea8582326809aef4e13cbeb7da2a5c76709
    Former-commit-id: 29847a775f685446b630a9ceee0ec52573acdf89
    [base.SLDPRT, base.STL, castor.SLDPRT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]
